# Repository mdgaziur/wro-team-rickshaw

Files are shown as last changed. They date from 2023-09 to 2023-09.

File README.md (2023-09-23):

# WRO Team: Rickshaw - _Anything for rickshaw!_

front-stylish
*Rickshaw in it's full glory*

## Table of Contents

- [Introduction](#introduction)
- [Repository Structure](#repository-structure)
- [Hardware Components](#hardware-components)
- [Software](#software)
- [Design decisions](#design-decisions)
- [Hardware Setup](#hardware-setup)
- [Software Setup](#software-setup)
- [The Journey](#the-journey)

## Introduction

This repoository contains the engineering materials for building the vehicle designed by team Rickshaw for the 
WRO 2023 Future Engineers category. The list of hardware components, details about the software that powers
the vehicle and design decisions are given here.

### Naming

The naming of the team is quite random. Our vehicle is called "Rickshaw"(ironically). And the motto _"Anything
for rickshaw!"_ signifies that we can do anything for the "Rickshaw" so that it works the best.

### The Team

The team consists of 3 very passionate students who are aiming to change Bangladesh through the next technological
revolution. This team is quite lucky to have a really helpful coach who's always coming up with ways to make the
best performing vehicle.

### Team Members
- Al Mubin Khan Nabil [@nirobnabil](https://github.com/nirobnabil) (Coach)
- MD Gaziur Rahman Noor [@mdgaziur](https://github.com/mdgaziur)
- Ibrahim Al Syed [@ibrahimalsyed60](https://github.com/ibrahimalsyed60)
- Abdus Sami Mohammad Adil [@adilahmed81](https://github.com/adilahmed81)

## Repository Structure

- `schematics`: Contains breadboard circuit image, schematic and a fritzing file containing the schematic of the vehicle
- `src`: Contains the source code to both software modules
- `team-photos`: Contains one funny and one normal photo of the team
- `vehicle-photos`: Contains photos of the vehicle from top, bottom, left, right, front and back side
- `video`: Contains `video.md` containing a link to the video demonstrating the vehicle

## Hardware Components

- Raspberry PI
- PI Camera
- Arduino Mega
- Buck Converter (x2)
- Breadboard
- 11.1V 3S 1500mAh LiPo Battery
- HC-SR04 Sonar Sensor (x3)
- DC Motor (x3)
- L293D Motor Driver
- Switch
- Push Button

The PI and the motor driver(and the motors) are powered by the LiPo battery. As we're connecting the Arduino
to the PI for serial communication, it gets the necessary power from the PI. The PI and the sonar sensors get
powered by two separate buck converters for the most efficient result.

## Software

The software of this vehicle is separated into two modules. One module runs on the Raspberry PI and does
object detection. After detecting objects, it sends necessary data to the Arduino using serial communication.
The module running on the Arduino receives the data and controls the vehicle accordingly. 

### Module 1: Object detection

This part of the software is written in Python 3. It mainly uses OpenCV to detect objects in the track. For detection,
it makes use of the LAB color space which has a dedicated channel for red and green colors. Because of this, detecting
these colors is really simplified. The module just has to check for two different thresholds each tuned for red and green
color detection to detect the red cubes and green cubes. After detecting the objects, it has to know which one is the closest
if there are multiple cubes. For this, the code calculates the area of the object and then compares them. The nearest one is
the one with the biggest area. Depending on the color of the cube, it sends 'L' or 'R' through serial communication. When
nohting is detected, 'N' is sent.

### Module 2: Arduino code

This part of the software controls the vehicle. To do this, it works with inputs from 3 ultrasonic sensors and
from the Raspberry PI. The Arduino follows an algorithm to control the vehicle.

The following algorithm is followed during the open challenge round:

1. Check if the vehicle is closer to the front wall than it is supposed to. Else, jump to 4.
2. If yes, check if the left wall is closer or the right wall.
3. If left wall is closer, turn right. Otherwise, turn left.
4. Check if the left wall or the right wall is closer.
5. Depending on that, go left or right slightly to make sure that the vehicle is centered.

Due to some hardware caused inconsistencies, there are some extra checks to make sure that the vehicle less
affected.

The following algorithm is followed during the obstacle challenge round:

1. Check if the vehicle is closer to the front wall than it is supposed to. Else, jump to 4.
2. If yes, check if the left wall is closer or the right wall.
3. If left wall is closer, turn right. Otherwise, turn left.
4. Move slightly to left or right depending on the detected object's color if any is detected. Otherwise jump to 5.
5. Check if the left wall or the right wall is closer.
6. Depending on that, go left or right slightly to make sure that the vehicle is centered.

## Design Decisions

Certain design decisions have been taken to make sure the vehicle works in the most optimal way and based on the availability
of parts in our region.

### The usage of Raspberry PI for object detection

We've chosen this component because of it's extensibility and customizability. Raspberry PI is powered by Linux. So, we can tweak
it as much as we want to match the optimal settings for operating the vehicle. Such tweakings include(but not limited to): console
mode for reducing CPU load during object detection, adding necessary softwares/libraries for image recognitions.

This SBC(aka. Single Board Computer) can be used to directly do serial communication with the Arduino Mega to send object detection data through USB connection. 
This allows us to avoid using complex circuitries for communication between PI and Arduino. The VNC and SSH capabilities of PI also allowed
us to easily do software development of the vehicle directly through a single interface. This reduced the amount of disconnecting and 
reconnecting stuff for debugging and fixing issues.

### Not using any camera with object detection capability

We've not chosen to bother using any camera with object detection on our vehicle. This is primarily due to such components not being available
in our region. However, the Arduino Mega is coded in such way that such components can be easily integrated with minimal changes to the code.

### The usage of Arduino Mega

Arduino Mega has just the right capability for a project like this. It has the right amount of processing power, memory and pins that make it
the best choice for this vehicle.

### The usage of an RC car as the chassis instead of a custom built one

This decision has been partly influenced by the scarcity of 3D printing in our region and partly by the ease of reproducability. Using an RC
car as the chassis allowed us to get around the issue of not being able to do 3D printing or using CNC to build a custom chassis. This has
also greatly simplified the development process.

### The usage of two motors to drive the vehicle forwards or backwards

The motor in the RC car's chassis can't generate enough torque to move the vehicle forward or backward. To remedy this, we've come up with a
design where two mechanically conncted DC motors. These generate enough torque to move the vehicle.

## Hardware setup

Firstly, solder jumper wires with appropriate colors to the buck converters. Female jumper wires are preferred for OUT+ and OUT- and male
jumper wires are preferred for IN+ and IN-.

Then, Make sure you have a decently sized RC car chassis. Put the motor driver, the buck converters, the battery, the ultrasonic sensors
and a voltage rail on the bottom chassis. You may want to cut out the AAA battery compartment out of the chassis to save space. Then put 4 hex 
extenders or anything tall enough on the four holes where screws were located previous. These are located on the 4 corners of the chassis.

For the second "floor", remove everything from the chassis first. Cut out the AAA battery compartment for saving space. Make a hole on the chassis. This is 
where we'll route all the cables from the bottom chassis to the top chassis. Put the Raspberry PI, Arduino Mega, PI Camera, and a voltage
rail there. You may refer to the vehicle pictures for help.

Before putting the top chassis on top of the extenders, connect everything based on the
schematics using jumper wires but do not connect the PI to the buck converter yet. Connect the bottom voltage rail to the battery and check whether
the lights of the buck converter and the motor driver are turned on or not. If they're turned on, everything's good. If not, immediately disconnect
the battery and check every connection. The most common mistake is wrong polarity. This can be checked by checking whether any wire has become hot or
not.

If everything's ok, connect the battery and then connect your multimeter to the OUT+ and OUT- pads of the buck converter. Slowly turn the screw like
thing on the blue part of the buck converter to adjust the output voltage. You should stop when your multimeter reads 5V. Now connect the buck converter
to the Raspberry PI and put the top chassis on top of the bottom chassis. Repeat the same for the buck converter for the sonar sensors.

## Software setup

We'll start by uploading the second module of our program to the Arduino Mega which controls the vehicle. Follow the following steps to upload the
program:

- Download and install Arduino IDE (if you already don't have it installed)
- Open `src/module_2_open_challenge/module_2_open_challenge.ino` in the IDE
- Connect your Arduino Mega to your computer. Depending on your operating system, you may have to follow additional steps.
- Press the button with "=>" icon located on top left to upload the program to your Arduino Mega.

Now, let's set up our Raspberry PI for the object detection code. First install Raspbian OS onto a memory card. Follow
[this tutorial](https://www.raspberrypi.com/documentation/computers/getting-started.html) for more info. You should
not install the full version of Raspbian OS as it's bloated with softwares that aren't really necessary for our job.
The base version of the OS which is 0.8GB in size is recommended. You also must install the `32-bit` version of this 
OS because the PI camera doesn't work on 64-bit Raspbian OS.

After installing Raspbian OS, we need to enable `Legacy Camera`. First, connect a monitor with an HDMI cable to your
Raspberry PI. Now, boot up your Raspberry PI by connecting it to any mobile phone charger. After it boots up, follow
along with the setup screen. After finishing that, open up terminal and run `sudo raspi-config`. Then, using arrow keys,
head to `Interfaces` option. Now go to `Legacy Camera` and enable that. Finally go back to main menu and navigate to `Finish`
and press enter. When it asks for rebooting, press `Yes`. 

After restarting, run the following command to install the necessary softwares for image recognition:

```sh
sudo apt update && sudo apt install python-opencv && pip3 install imutils "picamera[array]" pyserial
```

Now, connect your camera to the Raspberry PI. After that, clone this repository into your PI and run the code inside `src/module_1/module_1.py` using the following
command:

```sh
python src/module_1/module_1.py
```

If everything's okay, you should see `No detection` on the terminal. Hold a green or a red object for testing. Now exit the program by pressing Ctrl+C.

Let's add the script to startup so that we don't have to start it manually all the time. Run the following command first:

```sh
sudo nano /etc/rc.local
```

Add the following line before `exit 0` (Assuming you cloned the repository on the home folder and the username is `pi`):

```sh
python /home/pi/wro-team-rickshaw/src/module_1/module_1.py
```

And you're done with software setup! Now connect the Arduino to the Raspberry PI and you're ready to go!

# The Journey

The journey to building the vehicle have been "rough", to say the least. We've faced extreme amounts of friction due to issues such as low availability of hardware, lack of certain services like 3D printing, etc.

The journey began with two of the teammates(MD Gaziur Rahman Noor and Syed Al Ibrahim) meeting each other through the help of the coach. We've started to plan out how we might make the final product. For an extra hand, Noor added his fellow classmate and close friend. Despite his enthusiasm and active willingness to cooperate, he had to leave the team due to extreme academic pressure. So, another friend of Noor, Adil was added. 

Initially it was planned that we'd do a 3D printing of our custom chassis. However, the lack of 3D printing service forced us to ditch that idea. This resulted in a huge amount of time being wasted. Fast forward to around 14 days before the contest, we've decided to make use of RV car's chassis. 

But then, we've got struck with another issue. The steering system of that chassis wouldn't work properly at all. Because of that, we had to get another one and design our vehicle once again. Hopefully that's the first and last design, right? right? 🥲

We kept hitting issues after issues and we couldn't solve them in time efficient way due to lack of availability of certain components. Our Arduino Mega had an already blown up voltage regulator so VIN wouldn't work. That was a massive stab in the back. Couple that with the fact that the PI would restart itself randomly, it was a truly **rough** joirney. But at least we've been able to make something, get new experiences and have nice memories :^)

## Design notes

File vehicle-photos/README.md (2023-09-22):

# Vehicle photos

## Front

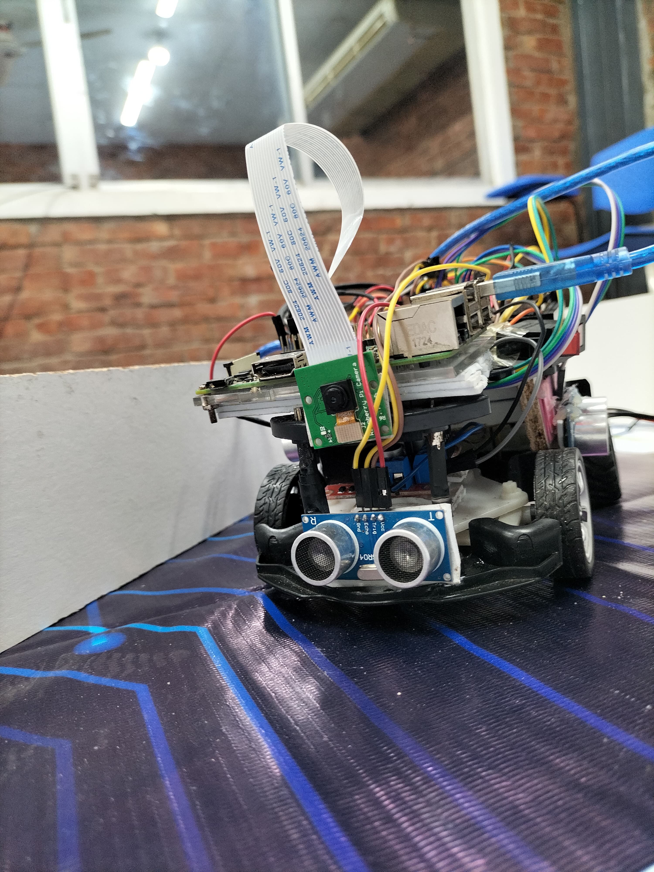
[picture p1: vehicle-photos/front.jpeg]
front


## Back

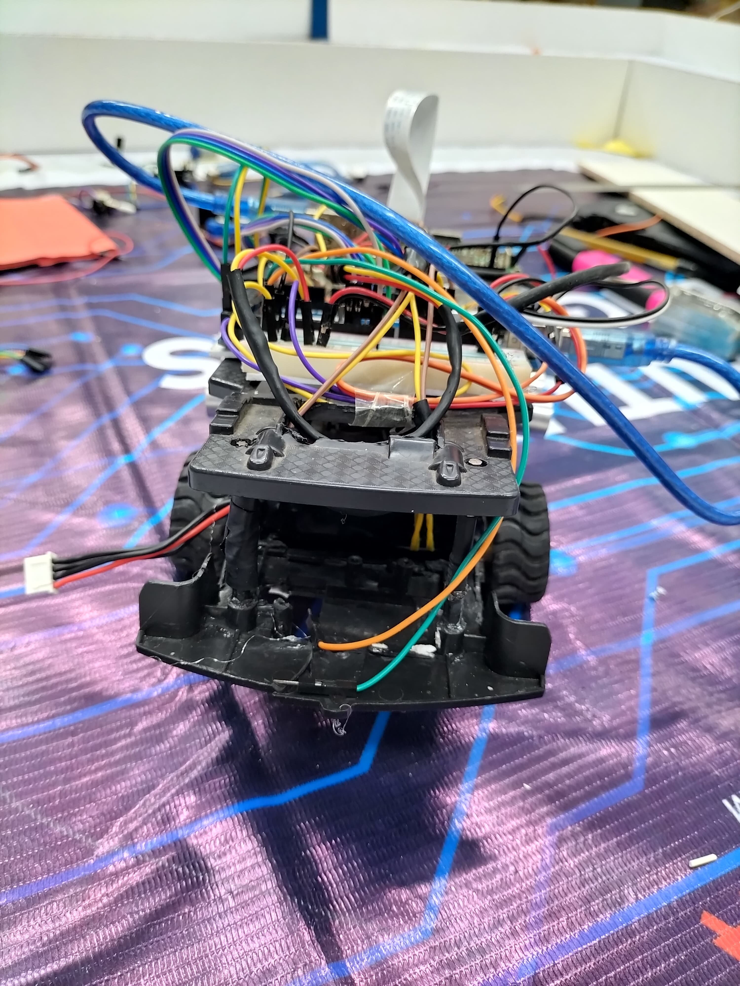
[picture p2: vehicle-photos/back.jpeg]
back


## Left

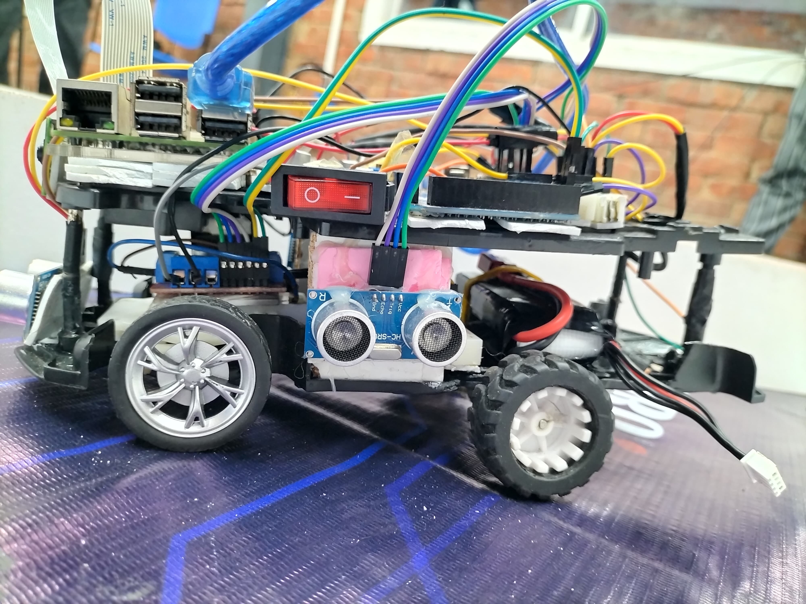
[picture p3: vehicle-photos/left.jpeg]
left


## Right

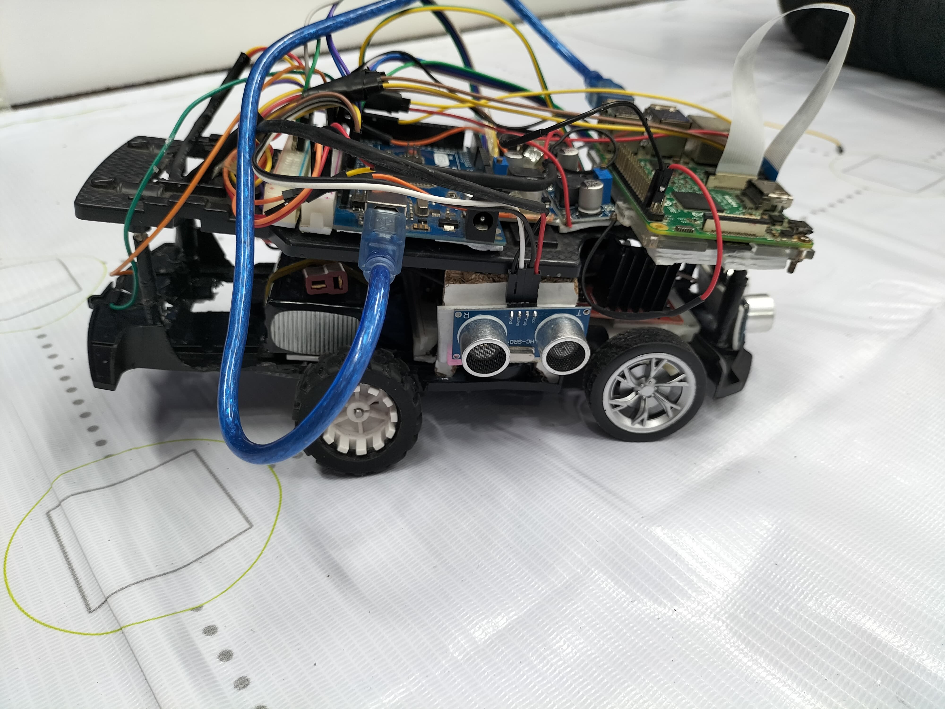
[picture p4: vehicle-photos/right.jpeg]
right


## Top

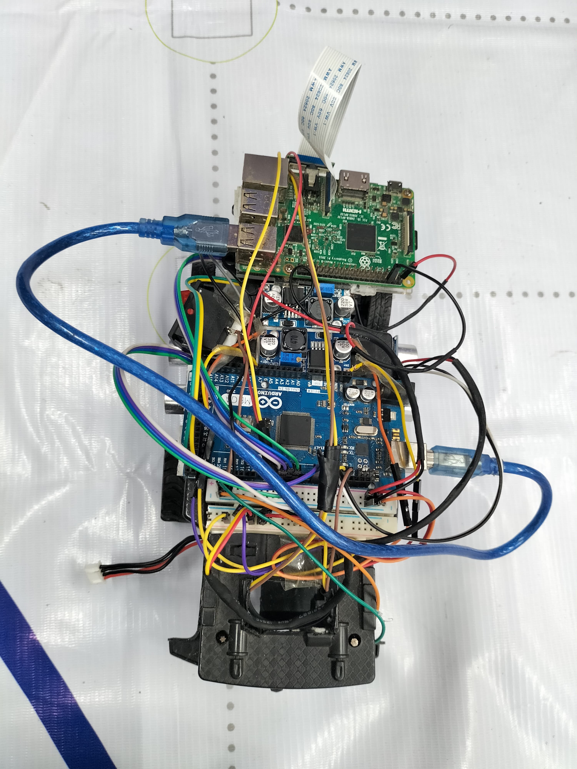
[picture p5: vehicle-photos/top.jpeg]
top


## Bottom

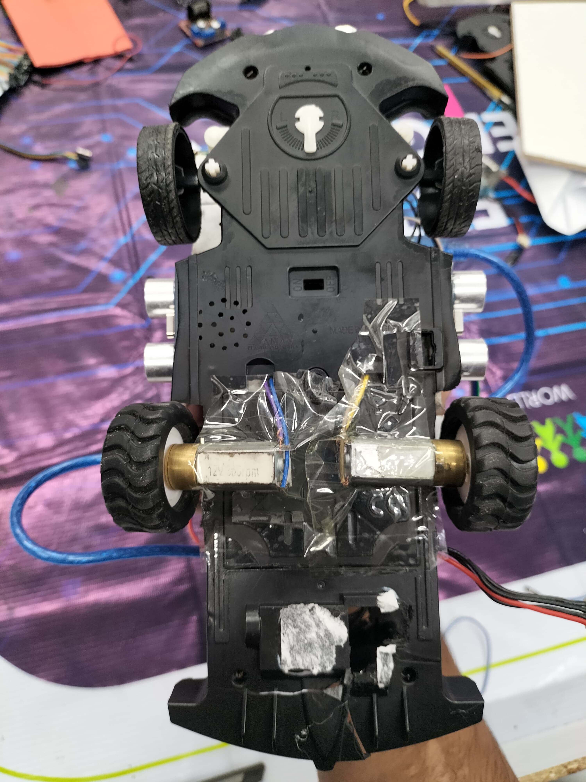
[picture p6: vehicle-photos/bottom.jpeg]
bottom


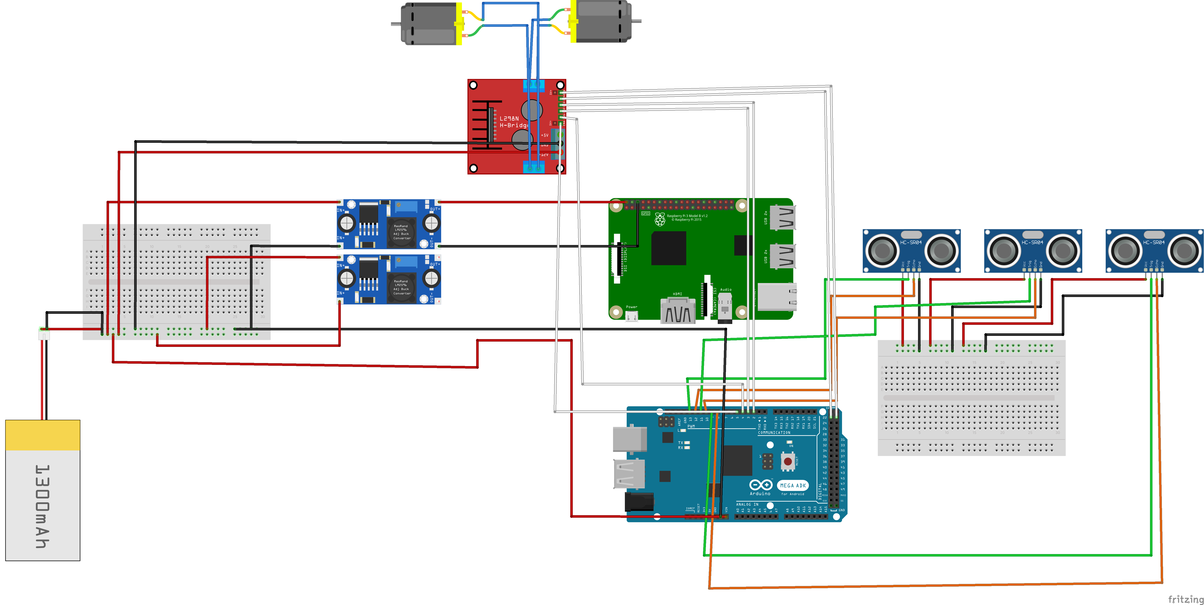
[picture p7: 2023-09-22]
schematics/breadboard_circuitry.png

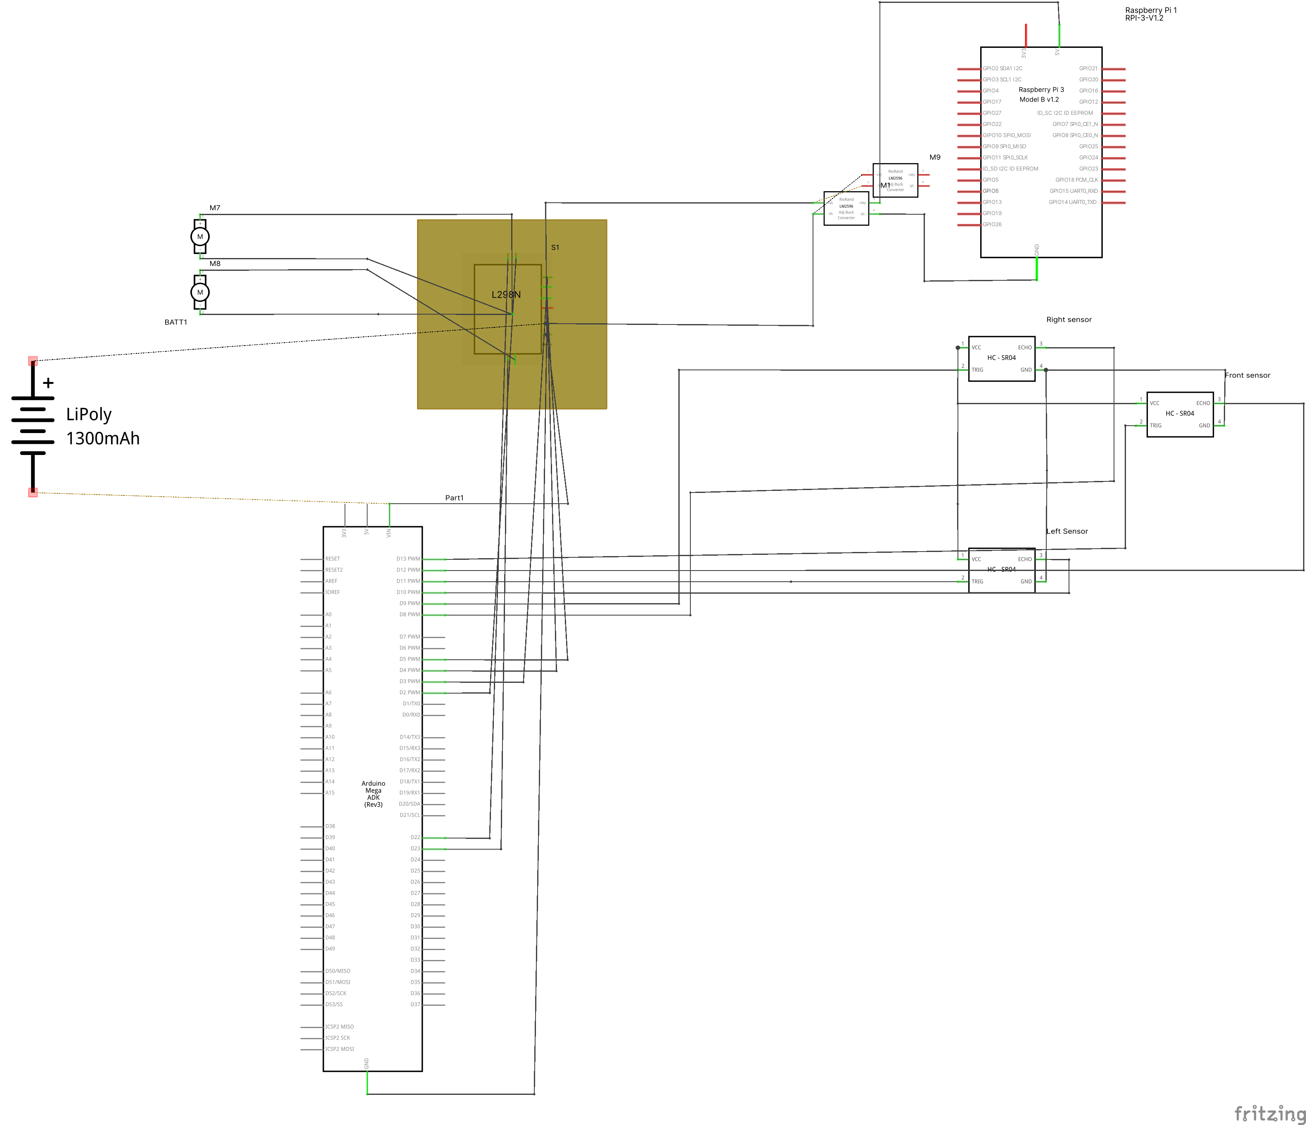
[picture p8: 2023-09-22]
schematics/schematic.png

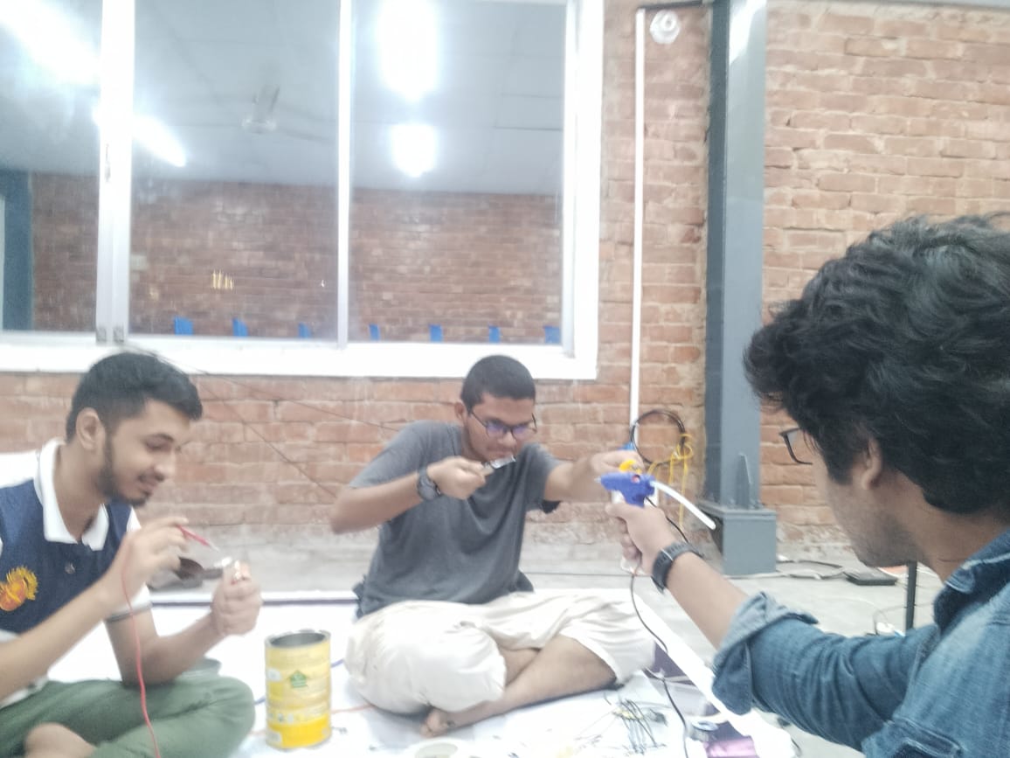
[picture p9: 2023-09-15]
team-photos/funny.jpeg

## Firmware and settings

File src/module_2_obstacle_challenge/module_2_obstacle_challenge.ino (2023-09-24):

#include <NewPing.h>

// Ultrasonic sensors
#define FRONT_T 13              // Trigger pin of the front ultrasonic sensor
#define FRONT_E 12              // Echo pin of the front ultrasonic sensor
#define RIGHT_T 11              // Trigger pin of the right ultrasonic sensor
#define RIGHT_E 10              // Echo pin of the right ultrasonic sensor
#define LEFT_T   9              // Trigger pin of the left ultrasonic sensor
#define LEFT_E   8              // Echo pin of the left ultrasonic sensor

// Motor driver pins
#define ENA      5              // Enable pin for the steering motor
#define IN2      4              // Pin1 of the steering motor
#define IN3      3              // Pin2 of the steering motor
#define ENB     23              // Enable pin for the driving motor
#define IN4      2              // Pin1 of the driving motor
#define IN5     22              // Pin2 of the driving motor

// Constants
#define NORMAL_DRIVE_POWER  255 // Power for normal driving operations
#define TURNING_DRIVE_POWER 175 // Power for driving motor when the vehicle is turning
#define STEERING_POWER      255 // Power for -+the steering motor
#define MIN_DIST_FROM_WALL   30 // Minimum allowed distance from wall(in cm)
#define TURN_DURATION_BASE  200 // Base value used as the duration for which the vehicle will turn.
// Will be multiplied by "turn duration factor" when turning.
#define MAX_DIST            300 // Maximum distance from any wall(in cm)
#define LR_ERROR_MARGIN       2 // Error margin while aligning the vehicle in the center among the right and left walls

#define BLOCK_UNITL_POSSIBLE_COLLISION(expr) \
      while (expr && ping_cm(front_sensor) > LR_ERROR_MARGIN && get_object_detection_status() == 'N') {}

int     turns = 0;              // Amount of turns the vehicle has completed
NewPing front_sensor(FRONT_T, FRONT_E, MAX_DIST);
NewPing right_sensor(RIGHT_T, RIGHT_E, MAX_DIST);
NewPing left_sensor(LEFT_T, LEFT_E, MAX_DIST);

void drive_forward() {
  digitalWrite(IN4, LOW);
  digitalWrite(IN5, HIGH);
}

void drive_backward() {
  digitalWrite(IN4, HIGH);
  digitalWrite(IN5, LOW);
}

void stop_driving() {
  digitalWrite(IN4, LOW);
  digitalWrite(IN5, LOW);
}

void steer_left() {
  digitalWrite(IN2, HIGH);
  digitalWrite(IN3, LOW);
}

void steer_right() {
  digitalWrite(IN2, LOW);
  digitalWrite(IN3, HIGH);
}

void stop_steering() {
  digitalWrite(IN2, LOW);
  digitalWrite(IN3, LOW);
}

char get_object_detection_status() {
  if (!Serial.available()) return 'N';

  return (char)Serial.read();
}

// Sets up motor located at given pins and sets given power(0-255) to the motor
void set_up_motor(int en, int in1, int in2, int power) {
  Serial.println(en);
  Serial.println(in1);
  Serial.println(in2);
  Serial.println(power);
  pinMode(en, OUTPUT);
  pinMode(in1, OUTPUT);
  pinMode(in2, OUTPUT);

  analogWrite(en, power);
}

int ping_cm(NewPing sensor) {
  int res = 0;
  int c = 5;
  while ( c-- ) res = max(res, sensor.ping_cm());
  if ( res == 0 ) res = 1000;
  return res;
}

void setup() {
  // Set baud rate as 9600 for Serial communication(mainly for debug purpose)
  Serial.begin(9600);
  Serial.println("٩(◕‿◕｡)۶ Konichiwaaaa");

  // Set up the steering motor and the driving motor
  set_up_motor(ENA, IN2, IN3, STEERING_POWER);
  set_up_motor(ENB, IN4, IN5, NORMAL_DRIVE_POWER);

  drive_forward();
}

void loop() {
  const char object_detection = get_object_detection_status();
  if (ping_cm(front_sensor) < MIN_DIST_FROM_WALL) {
    if (ping_cm(left_sensor) > ping_cm(right_sensor)) {
      steer_left();
    } else {
      steer_right();
    }

    while (ping_cm(front_sensor) < MIN_DIST_FROM_WALL) {}
    stop_steering();
  } else if (object_detection == 'L' && ping_cm(left_sensor) > MIN_DIST_FROM_WALL) {
    steer_left();
    while (ping_cm(left_sensor) > MIN_DIST_FROM_WALL) {
      if (ping_cm(front_sensor) < MIN_DIST_FROM_WALL) {
        break;
      }
    }
    steer_right();
    delay(200);
    stop_steering();
  } else if (object_detection == 'R' && ping_cm(right_sensor) > MIN_DIST_FROM_WALL) {
    steer_right();
    while (ping_cm(right_sensor) > MIN_DIST_FROM_WALL) {
      if (ping_cm(front_sensor) < MIN_DIST_FROM_WALL) {
        break;
      }
    }
    steer_left();
    delay(200);
    stop_steering();
  } else if (ping_cm(left_sensor) < MIN_DIST_FROM_WALL) {
    steer_right();
    BLOCK_UNITL_POSSIBLE_COLLISION(ping_cm(left_sensor) < MIN_DIST_FROM_WALL);
    stop_steering();
  } else if (ping_cm(right_sensor) < MIN_DIST_FROM_WALL) {
    steer_right();
    BLOCK_UNITL_POSSIBLE_COLLISION(ping_cm(left_sensor) < MIN_DIST_FROM_WALL);
    stop_steering();
  } else if (abs(ping_cm(left_sensor) - ping_cm(right_sensor)) > LR_ERROR_MARGIN) {
    if (ping_cm(left_sensor) > ping_cm(right_sensor)) {
      steer_left();
    } else {
      steer_right();
    }

    BLOCK_UNITL_POSSIBLE_COLLISION(abs(ping_cm(left_sensor) - ping_cm(right_sensor)) > LR_ERROR_MARGIN);
    stop_steering();
  }
}

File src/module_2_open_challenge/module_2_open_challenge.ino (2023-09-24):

#include <NewPing.h>

// Ultrasonic sensors
#define FRONT_T 13              // Trigger pin of the front ultrasonic sensor
#define FRONT_E 12              // Echo pin of the front ultrasonic sensor
#define RIGHT_T 11              // Trigger pin of the right ultrasonic sensor
#define RIGHT_E 10              // Echo pin of the right ultrasonic sensor
#define LEFT_T   9              // Trigger pin of the left ultrasonic sensor
#define LEFT_E   8              // Echo pin of the left ultrasonic sensor


// Motor driver pins
#define ENA     23              // Enable pin for the driving motor
#define IN2     22              // Pin1 of the driving motor
#define IN3      2              // Pin2 of the driving motor
#define ENB      5              // Enable pin for the steering motor
#define IN4      4              // Pin1 of the steering motor
#define IN5      3              // Pin2 of the steering motor


// Constants
#define NORMAL_DRIVE_POWER  200 // Power for normal driving operations
#define TURNING_DRIVE_POWER 200 // Power for driving motor when the vehicle is turning
#define STEERING_POWER      255 // Power for the steering motor
#define MIN_DIST_FROM_WALL   60 // Minimum allowed distance from wall(in cm)
#define TURN_DURATION_BASE  200 // Base value used as the duration for which the vehicle will turn.
                                // Will be multiplied by "turn duration factor" when turning.
#define MAX_DIST            1000 // Maximum distance from any wall(in cm)
#define LR_ERROR_MARGIN       3 // Error margin while aligning the vehicle in the center among the right and left walls(in cm)
#define TURN_STEERING_STOP_DELAY 700 // The delay which is required for the vehicle to be in perfect position after turn(in ms)
#define CRASH_THRESHOLD           20
#define CRASH_THRESHOLD2           10
#define TURN_THRESHOLD            60

NewPing left_sensor(LEFT_T, LEFT_E, MAX_DIST);
NewPing front_sensor(FRONT_T, FRONT_E, MAX_DIST);
NewPing right_sensor(RIGHT_T, RIGHT_E, MAX_DIST);

void drive_forward() {
  digitalWrite(IN2, HIGH);
  digitalWrite(IN3, LOW);
}

void drive_backward() {
  digitalWrite(IN2, LOW);
  digitalWrite(IN3, HIGH);
}

void stop_driving() {
  digitalWrite(IN2, LOW);
  digitalWrite(IN3, LOW);
}

void steer_left() {
  Serial.println("GOING LEFT");
  digitalWrite(IN4, HIGH);
  digitalWrite(IN5, LOW);
}

void steer_right() {
 
  Serial.println("GOING RIGHT");
  digitalWrite(IN4, LOW);
  digitalWrite(IN5, HIGH);
}

void stop_steering() {
  digitalWrite(IN4, LOW);
  digitalWrite(IN5, LOW);
}

void set_power(int power) {
  analogWrite(ENA, power);
}

// Sets up motor located at given pins and sets given power(0-255) to the motor
void set_up_motor(int en, int in1, int in2, int power) {
  pinMode(en, OUTPUT);
  pinMode(in1, OUTPUT);
  pinMode(in2, OUTPUT);

  analogWrite(en, power);
}

int ping_cm(NewPing sensor) {
  int res = 0;
  int c = 5;
  while( c-- ) res = max(res, sensor.ping_cm());
  if( res == 0 ) res = 1000;
  return res;
}


void setup() {
  // put your setup code here, to run once:
  Serial.begin(9600);

  set_up_motor(ENA, IN2, IN3, NORMAL_DRIVE_POWER);
  set_up_motor(ENB, IN4, IN5, STEERING_POWER);
  
}

void loop() {
  char bias = 'R';
  bool back_flag = 0;
  const int back_flag_thres = 10;
  while(1) {
    int f_dist = ping_cm(front_sensor);
    int l_dist = ping_cm(left_sensor);
    int r_dist = ping_cm(right_sensor);
    
    Serial.println(f_dist);
    Serial.println(l_dist);
    Serial.println(r_dist);
    Serial.println("-------");
    Serial.println("-------")
    
    if( l_dist < 8 || r_dist < 8 ) {
      stop_steering();
      drive_backward();
      delay(100);  
      continue;
    }
    
    if( f_dist < CRASH_THRESHOLD ) {
      if( r_dist < CRASH_THRESHOLD2 ) steer_right();
      else if( l_dist < CRASH_THRESHOLD2 ) steer_left();
      else stop_steering();
      drive_backward();
      delay(150);
      continue;
    }
    
    if( abs(l_dist - r_dist) > 0 ) {
      if( l_dist > r_dist ) steer_left();
      else steer_right(); 
      drive_forward();
      continue;
    }
    
    drive_forward();
    stop_steering();
  }
}

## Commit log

2023-09-15 Schematics: add schematics and breadboard circuitry image
    [vehicle_schematic.fzz]
2023-09-19 Module 2(Open Challenge V2): fix typo in comment
    [module_2_open_challenge_v2.ino]
2023-09-20 Module 2(Obstacle Challenge): change position of emotes (=^･ω･^=)
2023-09-20 Obstacle challenge: avoid hitting the front wall during avoidance
    [module_2_obstacle_challenge.ino]
2023-09-20 Obstacle challenge(bugfix): print mpu6050 status to serial
    [module_2_obstacle_challenge.ino]
2023-09-22 Open challenge: fine tune certain values and fix power consumption
    [module_2_open_challenge_v2.ino]
2023-09-22 Schematics: update schematics to match the new design
    [vehicle_schematic.fzz]
2023-09-24 Module 2(Open Challenge V2): reduce crash threshold
    [module_2_open_challenge_v2.ino]
